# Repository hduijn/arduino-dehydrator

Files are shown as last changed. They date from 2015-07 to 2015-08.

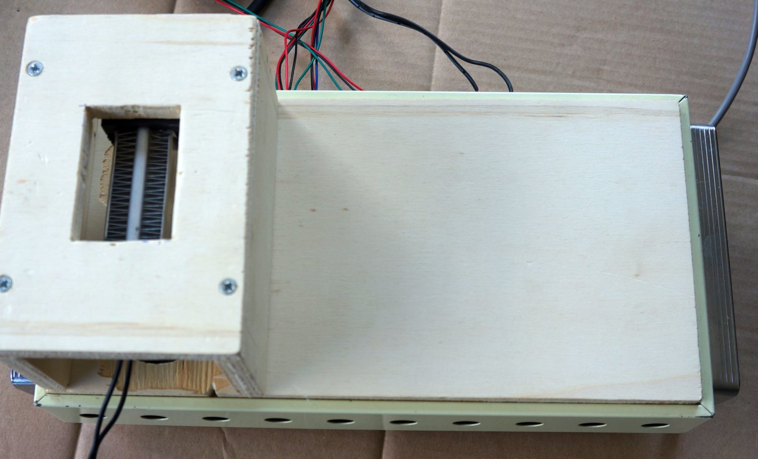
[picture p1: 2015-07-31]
Photos/bottom part construction.jpg

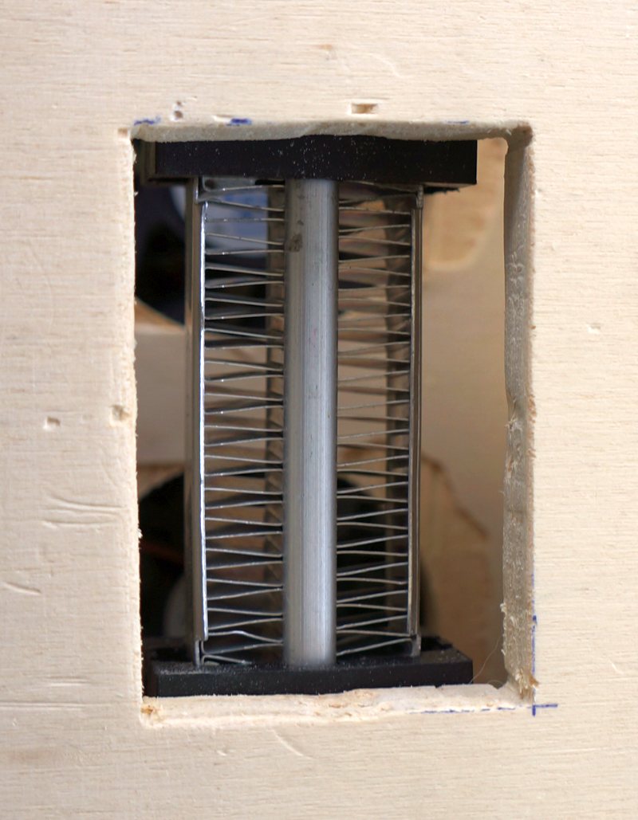
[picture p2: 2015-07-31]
Photos/PTC heater buildin.jpg

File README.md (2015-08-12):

# arduino-dehydrator
Dehydrator project based on Arduino

## Author

Author Name <hugovanduijn@gmail.com>

## Synopsis

Dehydrator project using Arduino for creating custom dehydrators. 

## Description

Using a rotary encoder it is possible to set a temperature between 25-75 degrees ( this can be modified in code ). When the switch of the rotary encoder is pressed then the program wil go in: "on" mode, this turns on the relays for the fans and starts to check the temperature and moisture using a KY-015 Sensor ( DHT11). Temperature and Moisture is displayed on the LCD and when the temperature is lower than the set temperature then the relay for the Heater will be turned on. 

If the heater is turned of then there will be a counter which will make sure there is a timeout of about 10 seconds before the heater can be turned on again, this is to avoid quick switching. 

2 x 0.47uF Capacitors are used on the CLK and DT pins to the ground for the rotary encoder, this removes debouncing and makes it possible to smoothly set the temperature. 

Key components used: 
- Solid State Relay : Omron G3MB-202P 2A ( can be switched by arduino without external power )
- PTC (Air) Heater Element : 100-300W 
- Arduino Uno
- Perf / prototype board
- KY-040 Rotary encoder
- KY-015 Temp + Moist sensor
- 1602 16x2 HD44780 Character LCD /w IIC/I2C Serial Interface 
- 60mm fans for airflow
- C14 inlet with 10A buildin fuse + switch
- 9V 35W powersupply for arduino and silent fan operation. 
- skilled woodworker / case builder

## Code

Code of the project can be found in arduinocode folder, code is still a bit messy but working. 

## Fritzing

Schema with parts is created in Fritzing, sketch and parts can be found in Fritzing folder. In the Fritzing/exports folder the dehydrator schema can be found in png format.

## 3D models 

3D models of LCD case in STL_3D folder, Files are modified from http://www.thingiverse.com/thing:30073
I've printed them with .2mm layer thickness and the case was a bit to small to fit rotary encoder and display properly. 
My advise is to print is slightly larger or just don't use the files for printing but only for inspiration.

## Parts

Parts can be purchased from http://www.makerwebshop.com see http://www.makerwebshop.com/kits/components-required-for-dehydrator-arduino-project for a link with almost all related parts.

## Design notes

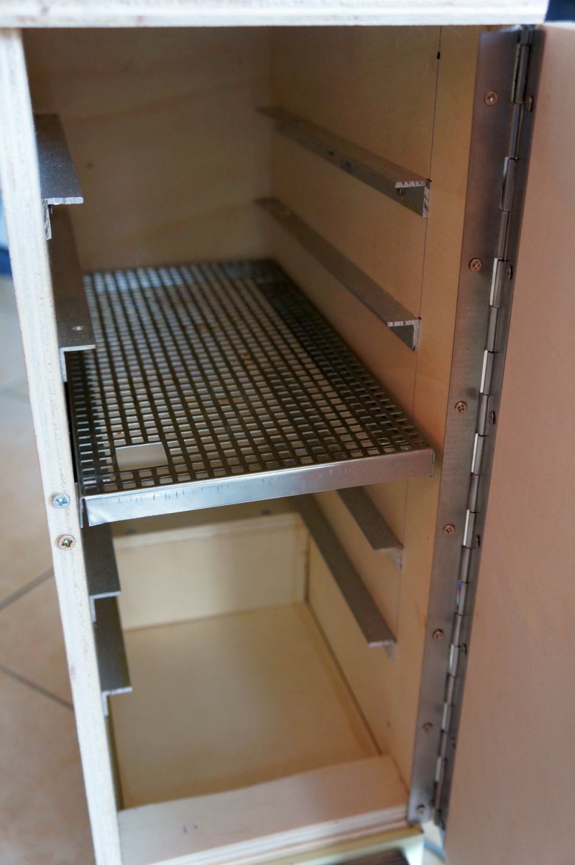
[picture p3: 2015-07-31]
Photos/inside look.jpg

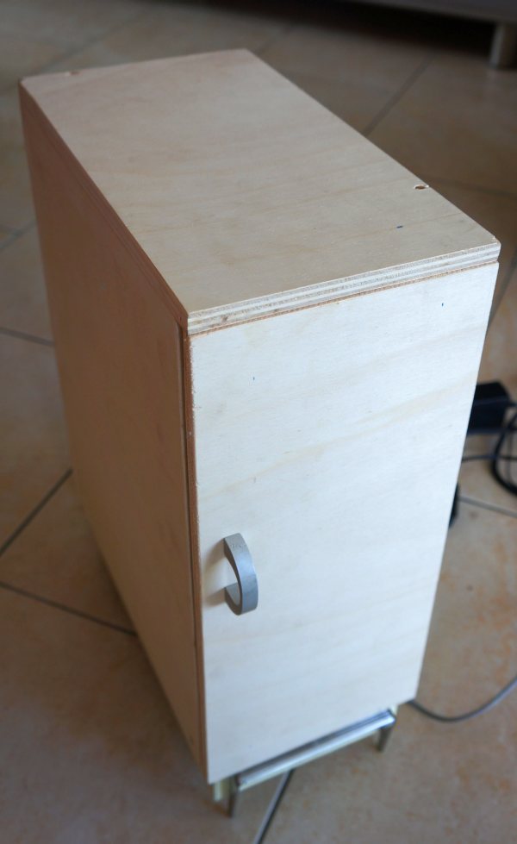
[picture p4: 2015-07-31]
Photos/Dehydrator fase 1.jpg

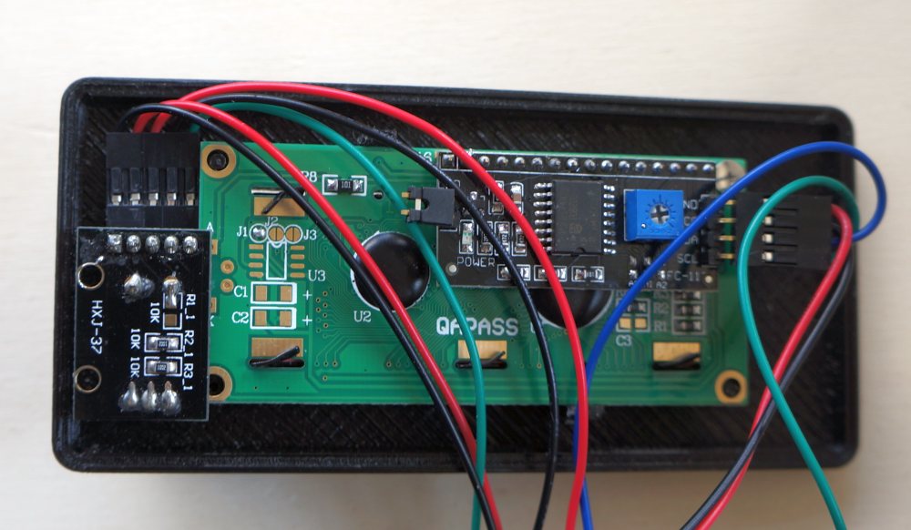
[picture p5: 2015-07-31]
Photos/display back.jpg

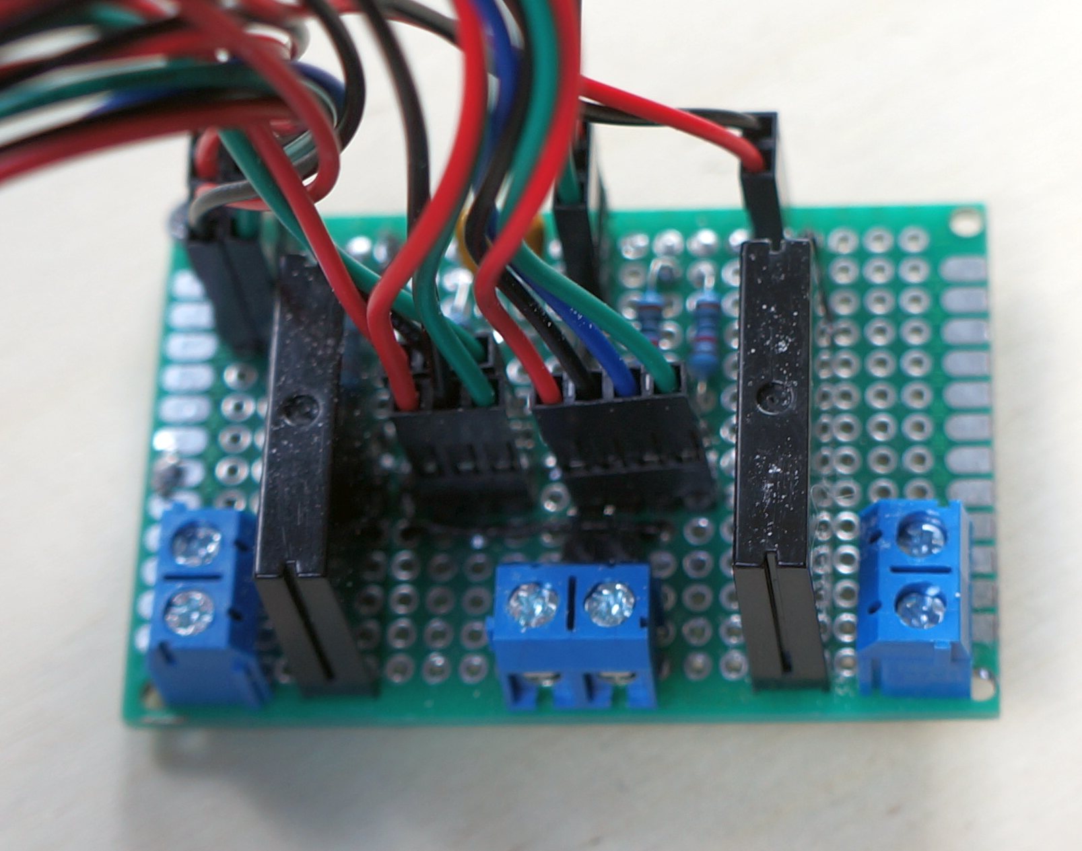
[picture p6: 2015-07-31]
Photos/perfboard top from back.jpg

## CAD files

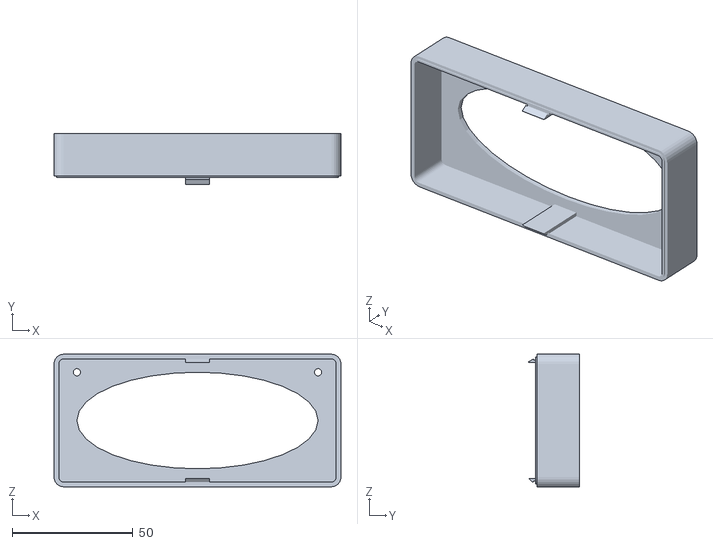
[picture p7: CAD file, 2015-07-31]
STL_3D/LCD Back.stl
119.0 x 21.2 x 55.0

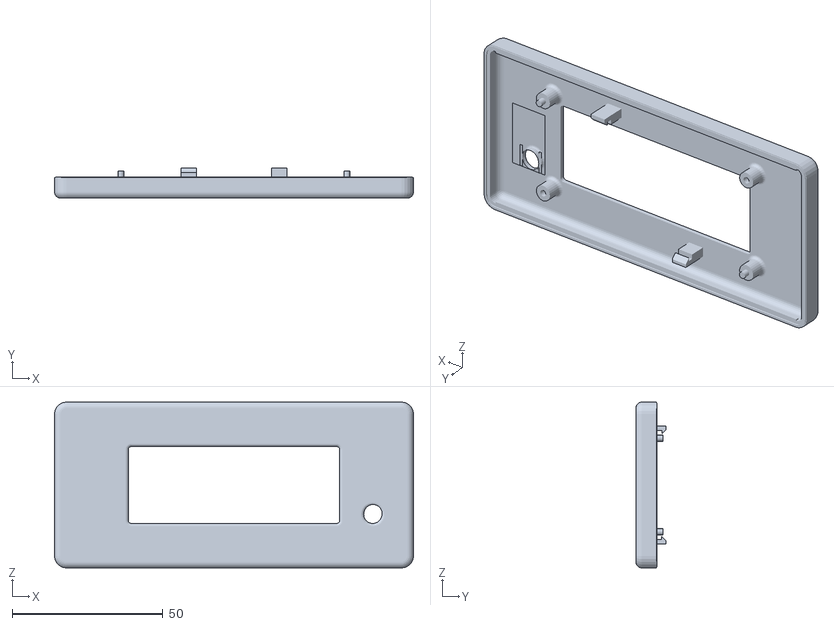
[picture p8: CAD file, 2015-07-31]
STL_3D/LCD front.stl
119.0 x 10.0 x 55.0

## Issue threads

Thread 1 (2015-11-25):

KY-040 has 3v3 connected to GND

wisemonkey, 2015-11-25:
Why is 3v3 pin connected to GND? Is it through potentiometer in encoder?
If that's the case can I somehow show them as disconnected in Fritzing so that while making PCB / Schematic I don't see 3v3 connected to GND (shorted) throughout my circuit.

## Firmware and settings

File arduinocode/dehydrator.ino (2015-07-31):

/*
** Arduino Dehydrator code for Dehydrator with 1602 LCD, temp sensor and rotary encoder
** by
** Hugo van Duijn
** http://www.makerwebshop.com
** LICENSE: GNU General Public License, version 3 (GPL-3.0)

** This example uses F Malpartida's NewLiquidCrystal library. Obtain from:
** https://bitbucket.org/fmalpartida/new-liquidcrystal
** I used version 1.2.1 https://bitbucket.org/fmalpartida/new-liquidcrystal/downloads/LiquidCrystal_V1.2.1.zip

** Written for and tested with Arduino 1.0
**
*/


#include <Wire.h>
#include <LCD.h>
#include <LiquidCrystal_I2C.h>


// defines for 1602 LCD
#define I2C_ADDR    0x3F 
#define BACKLIGHT_PIN     3
#define En_pin  2
#define Rw_pin  1
#define Rs_pin  0
#define D4_pin  4
#define D5_pin  5
#define D6_pin  6
#define D7_pin  7
                     

// Defines for rotary knob ky-040
volatile boolean TurnDetected;
volatile boolean up;

const int PinCLK=2;                   // Used for generating interrupts using CLK signal
const int PinDT=3;                    // Used for reading DT signal
const int PinSW=4;                    // Used for the push button switch

//more code for 1602 LCD 
void isr ()  {                    // Interrupt service routine is executed when a HIGH to LOW transition is detected on CLK
 if (digitalRead(PinCLK))
   up = !digitalRead(PinDT);
 else
   up = digitalRead(PinDT);
 TurnDetected = true;
}
int diff;
int n = 1;
int start = -1;
LiquidCrystal_I2C	lcd(I2C_ADDR,En_pin,Rw_pin,Rs_pin,D4_pin,D5_pin,D6_pin,D7_pin);

//Defines for KY015 DHT11 Temperature and humidity sensor 
int DHpin = 8;
byte dat [5];
byte read_data () {
  byte data;
  for (int i = 0; i < 8; i ++) {
    if (digitalRead (DHpin) == LOW) {
      while (digitalRead (DHpin) == LOW); // wait for 50us
      delayMicroseconds (30); // determine the duration of the high level to determine the data is '0 'or '1'
      if (digitalRead (DHpin) == HIGH)
        data |= (1 << (7-i)); // high front and low in the post
      while (digitalRead (DHpin) == HIGH); // data '1 ', wait for the next one receiver
     }
  }
return data;
}

// code for temp + moisture reading
void start_test () {
  digitalWrite (DHpin, LOW); // bus down, send start signal
  delay (30); // delay greater than 18ms, so DHT11 start signal can be detected
 
  digitalWrite (DHpin, HIGH);
  delayMicroseconds (40); // Wait for DHT11 response
 
  pinMode (DHpin, INPUT);
  while (digitalRead (DHpin) == HIGH);
  delayMicroseconds (80); // DHT11 response, pulled the bus 80us
  if (digitalRead (DHpin) == LOW);
  delayMicroseconds (80); // DHT11 80us after the bus pulled to start sending data
 
  for (int i = 0; i < 4; i ++) // receive temperature and humidity data, the parity bit is not considered
    dat[i] = read_data ();
 
  pinMode (DHpin, OUTPUT);
  digitalWrite (DHpin, HIGH); // send data once after releasing the bus, wait for the host to open the next Start signal
}


void setup()
{
  
  
// Initialise the Arduino data pins for OUTPUT, these are the 2 Solid State Relay Pins

  pinMode(10, OUTPUT);       
  pinMode(11, OUTPUT);      
  
// Set modes for rotaty encoder pins
 pinMode(PinCLK,INPUT);
 pinMode(PinDT,INPUT);  
 pinMode(PinSW,INPUT);
 pinMode (DHpin, OUTPUT);
 attachInterrupt (0,isr,FALLING);   // interrupt 0 is always connected to pin 2 on Arduino UNO
 Serial.begin (9600);
 Serial.println("Start");
 
// lcd setup
  lcd.begin (16,2); 

// Switch on the LCD backlight
lcd.setBacklightPin(BACKLIGHT_PIN,POSITIVE);
lcd.setBacklight(HIGH);
lcd.home (); // go home
lcd.setBacklight(HIGH);     // Backlight on
}

void loop()
{

 static long virtualPosition=0;    // without STATIC the rotary encoder does not count correctly!!!

        if (!(digitalRead(PinSW))) {        // check if pushbutton is pressed
            start = start * -1;            // if YES, then switch start mode. ( -1 = off, 1 = on )
            while (!digitalRead(PinSW)) {}  // wait til switch is released
            delay(10);                      // debounce
            Serial.println("Power Switch Event");        // Using the word RESET instead of COUNT here to find out a buggy encoder
            }
 if (virtualPosition < 25){ virtualPosition = 25; }  // min temp = 25
 if (virtualPosition > 75){ virtualPosition = 75; }  // max temp = 75
 if (TurnDetected)  {		   // do this only if rotation was detected
   if (up)
     virtualPosition++;
    else
     virtualPosition--;
     TurnDetected = false;          // do NOT repeat IF loop until new rotation detected
   }
   lcd.setCursor (0,1);  

// code when power is on
   if (start == 1){ 
     digitalWrite(10,HIGH);         // Turns ON FAN relays
     lcd.print("on ");                    // Print to LCD  on 
     start_test ();                        // check temp + moist
     delay (400);                        // Delay 400ms, 400ms still makes is possible to adjust temp during on.
       lcd.setCursor (0,0);           
       lcd.print("t:");                   // print info to lcd
       lcd.print (dat [2], DEC);
       lcd.print ("C("); 
       lcd.print (dat [0], DEC);
       lcd.print ("%) s:"); 
       lcd.print(virtualPosition);    // virtualPosition is the temp set by encoder
       diff = virtualPosition- dat [2];  // check difference between set temp and measured temp
       if (diff > 0){           // diff > 0 means set temp is higher than actual temp so start heating
         lcd.setCursor (8,1);   
         if (n < 20){                     // if  heater was turned off less than 20x400ms ago then don't start heating again but wait a moment and display TIMEOUT
           lcd.print(" TIMEOUT ");
           n=n+1;
         }else{
           digitalWrite(11,HIGH);   // Switch Relay 2 to start heating
           lcd.print(" HEATING ");      
           n=99;
         }
       } else {
         lcd.setCursor (8,1);         // if set temp is not higher than actual temp then switch HEATER Relay  off 
            digitalWrite(11,LOW);  
            lcd.print("         ");
         if (n==99){ n=0;}
         n=n+1;
       }
 } else {   // system is set to off
      digitalWrite(10,LOW);           // Turns OFF both relays and display info to LCD
      digitalWrite(11,LOW);  
       lcd.print("off");
          lcd.setCursor (0,0);
       lcd.print("t:");
       lcd.print (dat [2], DEC);
       lcd.print ("C("); 
       lcd.print (dat [0], DEC);
          lcd.print ("%) s:"); 
       lcd.print(virtualPosition);


 }
}

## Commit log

2015-07-31 First commit of dehydrator code
    [dehydrator.fzz]
2015-07-31 Initial upload of Fritzing and 3D files
    [LCD Back.stl, LCD front.stl, dehydrator.fzz]
